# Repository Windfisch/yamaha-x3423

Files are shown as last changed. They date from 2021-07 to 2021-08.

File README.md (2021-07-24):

Faderboard Controller for a Yamaha X3423
========================================

This project takes out the X3423 motorized faderboard from a Yamaha 01v96 mixer and lets you wire it
up via USB. Additionally, it will have a display for each two faders that can display information
such as the assigned control.

Features right now:
	- Fader values are sent and received via MIDI CCs 1-17; sending a CC via MIDI will move the
	  fader to the respective position.
	- Integrating position regulator allows precise movement of the faders (which would otherwise
	  stop a bit before the actual target position due to friction).
	- Faders can work continously or in discrete steps; CCs 71-87 control the number of steps (where
	  0 means "continuous").
	- Calibration data is stored to flash. Perform a calibration by sending CC 100.

Hardware setup
--------------

Use a 1.25 pitch FFC A ribbon cable with 34 pins (*Note: these are quite difficult to get, I bought
a 40-lane-cable and cut it down.*) to connect the PCB with the faderboard on CN001; either use the
proper connector (*not JST*) to connect J12 with CN002, or solder an appropriate connector/cables to
CN002. Connect J16 and J17 to a buck/boost converter accepting 16V and outputting +15V/-15V, e.g.
DD39AJPA (DD1912PA should work too) from your favourite chinese marketplace.

Be sure to simultaneously power up both the main PSU and the USB board for now.

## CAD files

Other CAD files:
case/front_laser/front_panel.FCStd

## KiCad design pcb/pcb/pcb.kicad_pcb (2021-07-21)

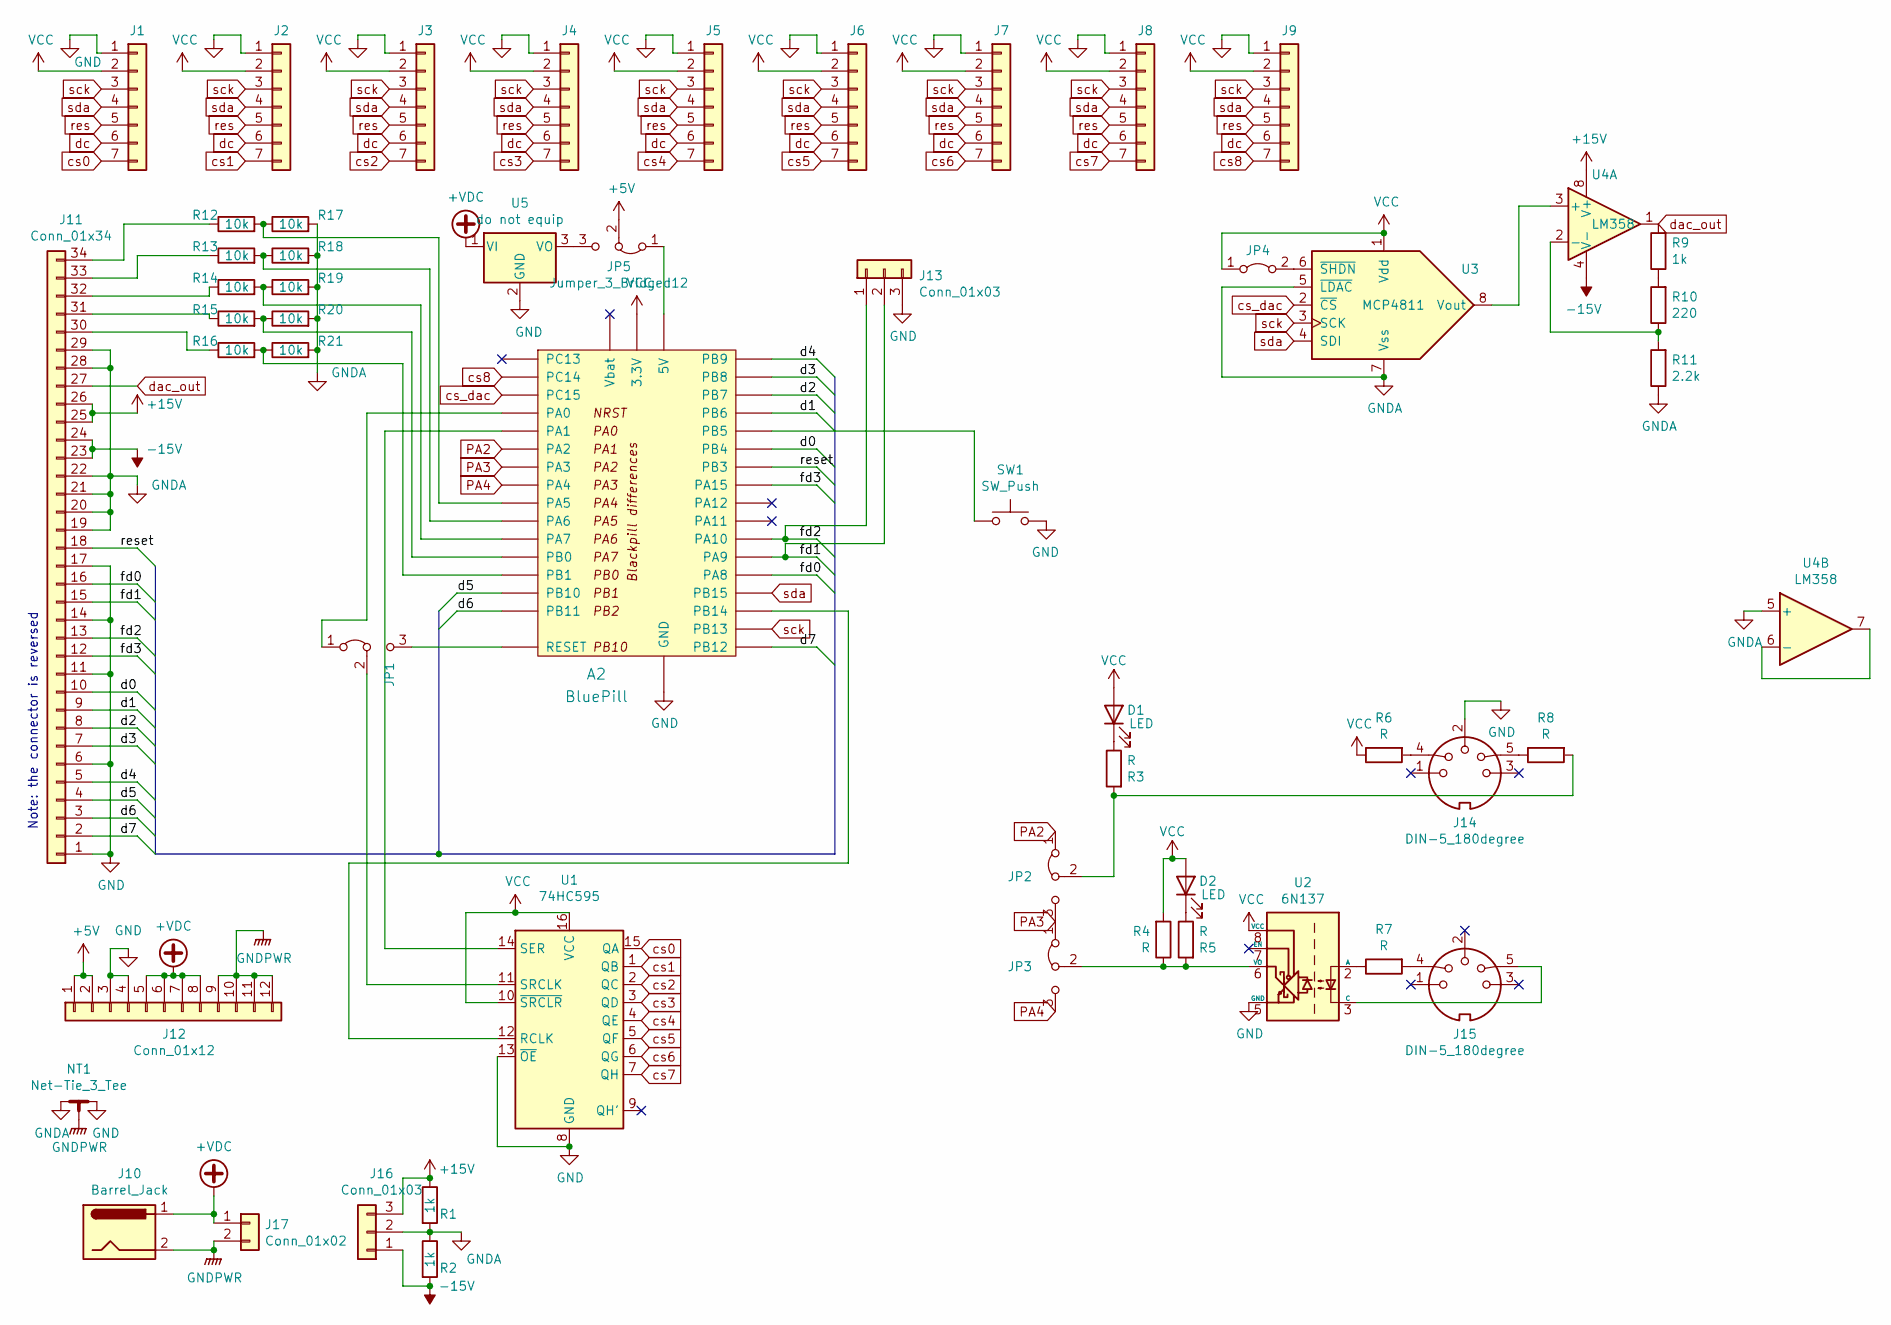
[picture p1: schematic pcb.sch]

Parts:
A2: BluePill; BLUEPILL-blackpill
D1, D2: LED; LED_D3.0mm_Horizontal_O1.27mm_Z2.0mm_IRBlack
J1, J2, J3, J4, J5, J6, J7, J8, J9: Conn_01x07; JST_XH_B7B-XH-A_1x07_P2.50mm_Vertical
J10: Barrel_Jack; BarrelJack_CUI_PJ-063AH_Horizontal
J11: Conn_01x34; Molex_52044_3445
J12: Conn_01x12; JST_PH_B12B-PH-K_1x12_P2.00mm_Vertical
J13: Conn_01x03; PinHeader_1x03_P2.54mm_Horizontal
J14, J15: DIN-5_180degree; DIN5
J16: Conn_01x03; JST_XH_B3B-XH-A_1x03_P2.50mm_Vertical
J17: Conn_01x02; JST_XH_B2B-XH-A_1x02_P2.50mm_Vertical
JP1, JP2, JP3, JP5: Jumper_3_Bridged12; SolderDipJumper3alt
JP4: Jumper_2_Bridged; SolderDipJumper2alt
NT1: Net-Tie_3_Tee; NetTie-3_SMD_Pad0.5mm
R1, R2, R9: 1k; R_0805_2012Metric
R3, R4, R5, R6, R7, R8: R; R_0805_2012Metric
R10: 220; R_0805_2012Metric
R11: 2.2k; R_0805_2012Metric
R12, R13, R14, R15, R16, R17, R18, R19, R20, R21: 10k; R_0805_2012Metric
SW1: SW_Push; SW_Tactile_Straight_KSL0Axx1LFTR
U1: 74HC595; DIP-16_W7.62mm
U2: 6N137; DIP-8_W7.62mm
U3: MCP4811; DIP-8_W7.62mm
U4: LM358; DIP-8_W7.62mm
U5: do not equip; TO-220-3_Horizontal_TabDown

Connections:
+5V: J12.1, J12.2, JP5.2 (C)
+15V: J11.25, J11.26, J16.3, R1.1, U4.8 (V+)
+VDC: J10.1, J12.5, J12.6, J12.7, J12.8, J17.1, U5.1 (VI)
-15V: J11.23, J11.24, J16.1, R2.2, U4.4 (V-)
/d0: A2.PB4, J11.10
/d1: A2.PB6, J11.9
/d2: A2.PB7, J11.8
/d3: A2.PB8, J11.7
/d4: A2.PB9, J11.5
/d5: A2.PB10, J11.4
/d6: A2.PB11, J11.3
/d7: A2.PB12, J11.2
/fd0: A2.PA8, J11.16
/fd1: A2.PA9, J11.15, J13.2
/fd2: A2.PA10, J11.13, J13.1
/fd3: A2.PA15, J11.12
/reset: A2.PB3, J11.18
GND: A2.G (GND), J1.1, J2.1, J3.1, J4.1, J5.1, J6.1, J7.1, J8.1, J9.1, J11.1, J11.6, J11.11, J11.14, J11.17, J12.3, J12.4, J13.3, J14.2, NT1.2, SW1.1, U1.8 (GND), U1.13 (~OE), U2.5 (GND), U5.2 (GND)
GNDA: J11.19, J11.20, J11.21, J11.22, J11.28, J11.29, J16.2, NT1.1, R1.2, R2.1, R11.1, R17.2, R18.2, R19.2, R20.2, R21.2, U3.5 (~LDAC), U3.7 (Vss), U4.5 (+)
GNDPWR: J10.2, J12.9, J12.10, J12.11, J12.12, J17.2, NT1.3
unnamed: A2.5V, JP5.1 (A)
unnamed: A2.NRST (RESET), JP1.3 (B)
unnamed: A2.PA0, JP1.1 (A)
unnamed: A2.PA1, U1.14 (SER)
unnamed: A2.PA5, R12.2, R17.1
unnamed: A2.PA6, R13.2, R18.1
unnamed: A2.PA7, R14.2, R19.1
unnamed: A2.PB0, R15.2, R20.1
unnamed: A2.PB1, R16.2, R21.1
unnamed: A2.PB5, SW1.2
unnamed: A2.PB14, U1.12 (RCLK)
unnamed: D1.1 (K), R3.1
unnamed: D2.1 (K), R5.1
unnamed: J11.30, R16.1
unnamed: J11.31, R15.1
unnamed: J11.32, R14.1
unnamed: J11.33, R13.1
unnamed: J11.34, R12.1
unnamed: J14.4, R6.2
unnamed: J14.5, R8.1
unnamed: J15.4, R7.2
unnamed: J15.5, U2.3 (C)
unnamed: JP1.2 (C), U1.11 (SRCLK)
unnamed: JP2.2 (C), R3.2, R8.2
unnamed: JP3.2 (C), R4.1, R5.2, U2.6 (VO)
unnamed: JP4.2 (B), U3.6 (~SHDN)
unnamed: JP5.3 (B), U5.3 (VO)
unnamed: R7.1, U2.2 (A)
unnamed: R10.1, R11.2, U4.2 (-)
unnamed: R9.1, R10.2
unnamed: U3.8 (Vout), U4.3 (+)
unnamed: U4.6 (-), U4.7
PA2: A2.PA2, JP2.1 (A)
PA3: A2.PA3, JP2.3 (B), JP3.1 (A)
PA4: A2.PA4, JP3.3 (B)
VCC: A2.3V3 (3.3V), D1.2 (A), D2.2 (A), J1.2, J2.2, J3.2, J4.2, J5.2, J6.2, J7.2, J8.2, J9.2, JP4.1 (A), R4.2, R6.1, U1.10 (~SRCLR), U1.16 (VCC), U2.8 (VCC), U3.1 (Vdd)
cs0: J1.7, U1.15 (QA)
cs1: J2.7, U1.1 (QB)
cs2: J3.7, U1.2 (QC)
cs3: J4.7, U1.3 (QD)
cs4: J5.7, U1.4 (QE)
cs5: J6.7, U1.5 (QF)
cs6: J7.7, U1.6 (QG)
cs7: J8.7, U1.7 (QH)
cs8: A2.PC14, J9.7
cs_dac: A2.PC15, U3.2 (~CS)
dac_out: J11.27, R9.2, U4.1
dc: J1.6, J2.6, J3.6, J4.6, J5.6, J6.6, J7.6, J8.6, J9.6
res: J1.5, J2.5, J3.5, J4.5, J5.5, J6.5, J7.5, J8.5, J9.5
sck: A2.PB13, J1.3, J2.3, J3.3, J4.3, J5.3, J6.3, J7.3, J8.3, J9.3, U3.3 (SCK)
sda: A2.PB15, J1.4, J2.4, J3.4, J4.4, J5.4, J6.4, J7.4, J8.4, J9.4, U3.4 (SDI)

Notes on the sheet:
Note: the connector is reversed

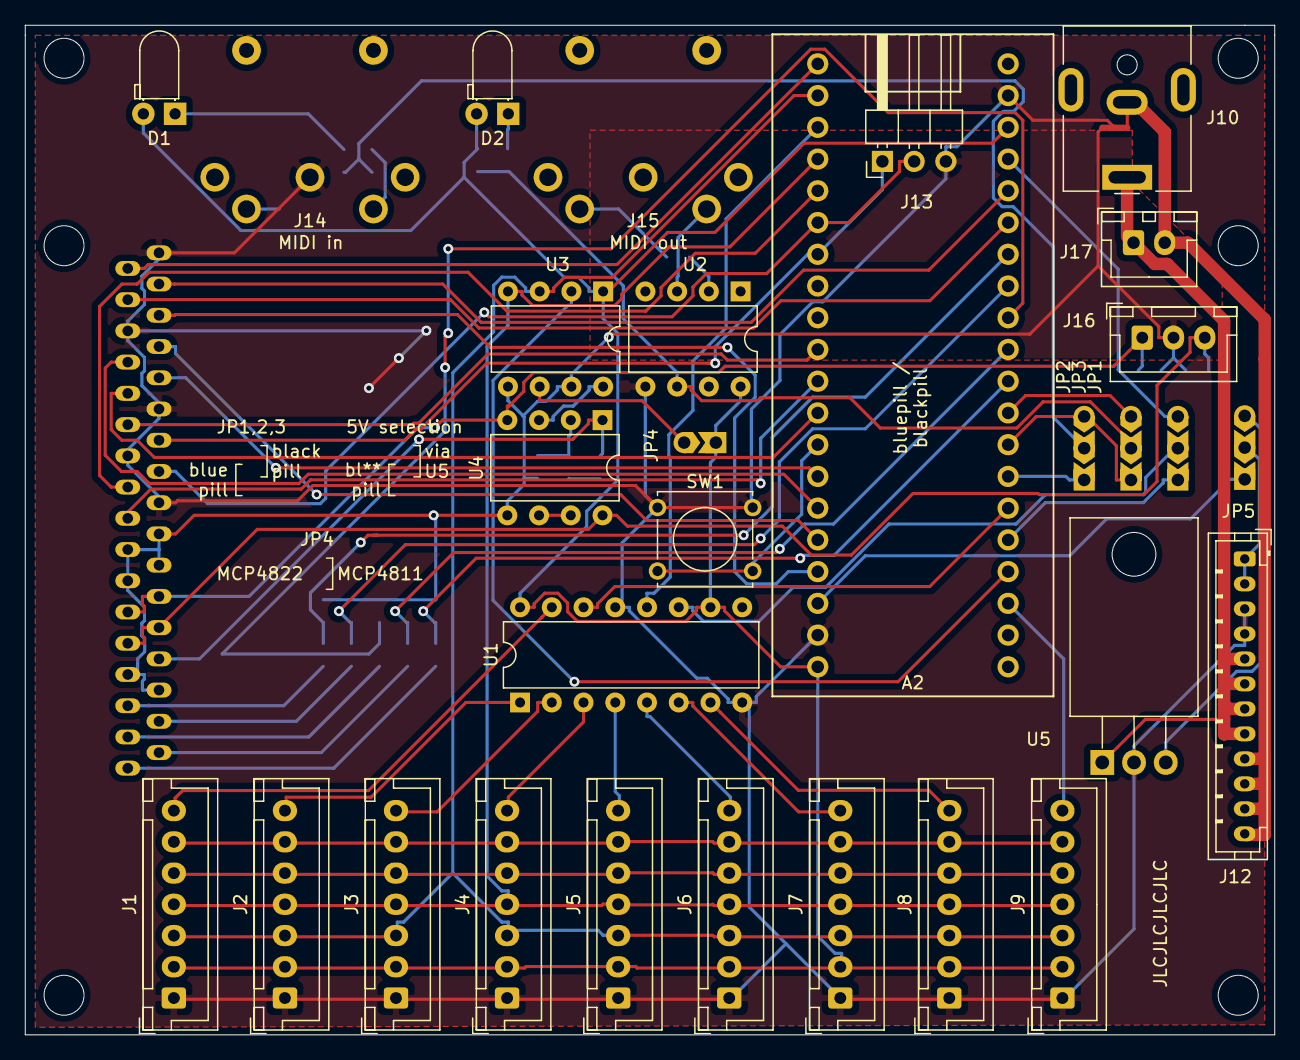
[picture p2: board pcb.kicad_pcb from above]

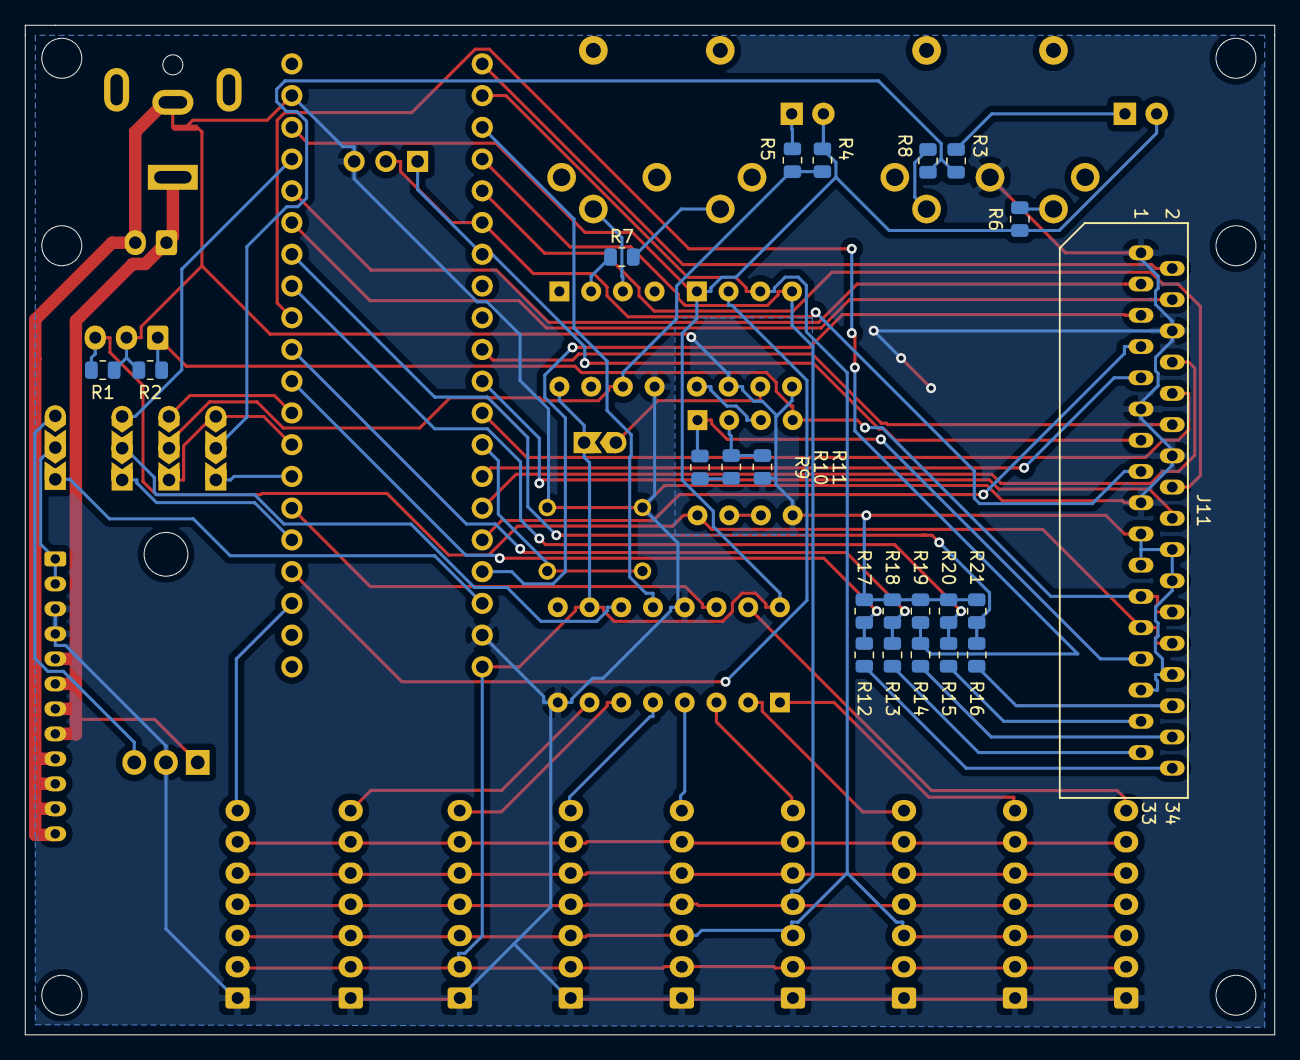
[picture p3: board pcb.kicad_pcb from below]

Board: 2 copper layers, 100.0 x 80.8 mm, 59 parts (22 on the bottom side), 71 nets.

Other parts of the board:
hole1, hole1#2, hole2, hole2#2, hole3, hole4: MountingHole_3.2mm_M3_DIN965

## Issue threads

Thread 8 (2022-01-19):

Fix laser layout

Windfisch, 2022-01-19:

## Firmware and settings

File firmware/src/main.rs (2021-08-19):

#![no_main]
#![no_std]

mod x3423;
mod fader;
use x3423::X3423;
use fader::Fader;

use embedded_hal::digital::v2::OutputPin;
use embedded_hal::digital::v1_compat::OldOutputPin;
use rtic::app;
use stm32f1xx_hal::gpio::{gpiob::*, gpioc::*, Input, Floating, Alternate, Output, PushPull, State};
use stm32f1xx_hal::spi;
use stm32f1xx_hal::timer;
use stm32f1xx_hal::prelude::*;
use stm32f1xx_hal::delay::Delay;
use stm32f1xx_hal::usb::{UsbBus, Peripheral, UsbBusType};
use stm32f1xx_hal::pac::TIM2;
use mcp49xx::Mcp49xx;
use mcp49xx::interface::SpiInterface;
use mcp49xx::marker::Resolution12Bit;
use mcp49xx::marker::DualChannel;
use mcp49xx::marker::Unbuffered;
use stm32f1xx_hal::time::Hertz;

use usb_device::prelude::*;

use micromath::F32Ext;


const BASE_CURRENT: f32 = 0.3; // Ampere
const FADER_CURRENT: f32 = 0.25; // Ampere. Note: this is only for slow movement and stall. Large jumps draw more current!
const CURRENT_LIMIT: f32 = 3.33; // Ampere.
const MAX_ACTIVE_FADERS: u16 = ((CURRENT_LIMIT - BASE_CURRENT) / FADER_CURRENT) as u16;
const MAX_ACTIVE_FADERS_DURING_CALIBRATION: u16 = 3;


#[panic_handler]
fn panic(_: &core::panic::PanicInfo) -> ! {
	use core::mem::MaybeUninit;
	cortex_m::interrupt::disable();

	let led: stm32f1xx_hal::gpio::gpioc::PC13<Input<Floating>> = unsafe { MaybeUninit::uninit().assume_init() };
	let mut reg = unsafe { MaybeUninit::uninit().assume_init() };
	let mut led = led.into_push_pull_output(&mut reg);
	loop {
		let mut blink_thrice = |delay: u32| {
			for _ in 0..3 {
				led.set_low().ok();
				cortex_m::asm::delay(5000000*delay);
				led.set_high().ok();
				cortex_m::asm::delay(10000000);
			}
			cortex_m::asm::delay(10000000);
		};
		blink_thrice(1);
		blink_thrice(4);
		blink_thrice(1);
		cortex_m::asm::delay(10000000);
	}
}

#[derive(Clone, Copy, PartialEq)]
pub enum Calib
{
	Pending,
	Running,
	Idle
}

#[derive(Clone, Copy)]
pub enum FaderState {
	Idle,
	UserControlled,
	UserOverride,
	MidiControlledSlow,
	MidiControlledJump
}

#[derive(Clone, Copy)]
pub struct Queue {
	history: [u16; 64],
	pointer: usize,
	counter: u16
}

impl Queue {
	const SPARSITY: u16 = 24;
	pub const fn new() -> Queue { Queue { history: [0; 64], pointer: 0, counter: 0 } }

	fn u16_to_f32(value: u16) -> f32 {
		value as f32 / 65535.0
	}

	pub fn push(&mut self, value: f32) {
		if self.counter == 0 {
			self.history[self.pointer] = (value * 65535.0) as u16;
			self.pointer = (self.pointer + 1) % self.history.len();
		}
		self.counter = (self.counter + 1) % Self::SPARSITY;
	}
	pub fn delta(&self) -> f32 {
		Self::u16_to_f32(*self.history.iter().max().unwrap()) - Self::u16_to_f32(*self.history.iter().min().unwrap())
	}

	pub fn trend(&self) -> f32 {
		let most_recent_pointer = (self.pointer + self.history.len() - 1) % self.history.len();
		return Self::u16_to_f32(self.history[most_recent_pointer]) - Self::u16_to_f32(self.history[self.pointer]);
	}
}

#[derive(Copy,Clone)]
pub struct FaderStateMachine {
	state: FaderState,
	old_setpoint: f32,
	stable_timer: u32,
	jump_count: u32,
	measured_history: Queue,
	setpoint_history: Queue,
}

pub struct FaderResult {
	pub fader_move_target: Option<f32>,
	pub midi_send_value: Option<f32>
}

trait Signum {
	fn signum(self) -> Self;
}

impl Signum for f32 {
	fn signum(self) -> f32 {
		if self > 0.0 { return 1.0; }
		else if self < 0.0 { return -1.0; }
		else { return 0.0; }
	}
}

impl FaderStateMachine {
	pub const fn new() -> FaderStateMachine {
		FaderStateMachine {
			state: FaderState::Idle,
			old_setpoint: 0.5,
			stable_timer: 0,
			jump_count: 0,
			measured_history: Queue::new(),
			setpoint_history: Queue::new()
		}
	}
	pub fn process(&mut self, setpoint: f32, measured: f32) -> FaderResult {
		let JUMP_THRESHOLD = 3.0;
		let SET_DEADZONE = 0.01;
		let SETPOINT_DEADZONE = 0.001;
		let ESCAPE_LIMIT = 0.2;
		let INPUT_DEADZONE = 0.05;
		let INPUT_DEADZONE_WHEN_MIDI_CONTROLLED = 0.15;
		let CAPTURE_ZONE = 0.06;
		let STABILIZE_TIMEOUT = 500;
		let JUMP_TIMEOUT = 2000;

		self.measured_history.push(measured);
		self.setpoint_history.push(setpoint);

		if (setpoint - measured).abs() < CAPTURE_ZONE {
			self.stable_timer = self.stable_timer.saturating_add(1);
		}
		else {
			self.stable_timer = 0;
		}

		let setpoint_diff = (self.old_setpoint - setpoint).abs();
		if setpoint_diff > SETPOINT_DEADZONE {
			self.stable_timer = 0;
			self.old_setpoint = setpoint;
		}

		match self.state {
			FaderState::Idle => {
				if setpoint_diff >= JUMP_THRESHOLD {
					self.state = FaderState::MidiControlledJump;
					self.jump_count = 0;
				}
				else if setpoint_diff > SETPOINT_DEADZONE {
					self.state = FaderState::MidiControlledSlow;
				}
			
				if (setpoint - measured).abs() >= ESCAPE_LIMIT {
					self.state = FaderState::UserOverride;
					self.measured_history.push(1.0);
					self.measured_history.push(0.0);
				}
				else if (setpoint - measured).abs() >= INPUT_DEADZONE {
					self.state = FaderState::UserControlled;
					self.measured_history.push(1.0);
					self.measured_history.push(0.0);
				}
				
				FaderResult {
					fader_move_target: None,
					midi_send_value: None
				}
			}
			FaderState::MidiControlledSlow => {
				if setpoint_diff >= JUMP_THRESHOLD {
					self.state = FaderState::MidiControlledJump;
					self.jump_count = 0;
				}
				if self.stable_timer >= STABILIZE_TIMEOUT {
					self.state = FaderState::Idle;
				}
				if (setpoint - measured).abs() >= ESCAPE_LIMIT {
					self.state = FaderState::UserOverride;
					self.measured_history.push(1.0);
					self.measured_history.push(0.0);
				}
				else if (setpoint - measured).abs() >= INPUT_DEADZONE_WHEN_MIDI_CONTROLLED {
					self.state = FaderState::UserControlled;
					self.measured_history.push(1.0);
					self.measured_history.push(0.0);
				}

				FaderResult {
					fader_move_target: Some(setpoint),
					midi_send_value: None
				}
			}
			FaderState::MidiControlledJump => {
				if self.stable_timer >= STABILIZE_TIMEOUT {
					self.state = FaderState::Idle;
				}
				if self.jump_count >= JUMP_TIMEOUT {
					self.state = FaderState::Idle;
				}
				self.jump_count += 1;

				FaderResult {
					fader_move_target: Some(setpoint),
					midi_send_value: None
				}
			}
			FaderState::UserControlled => {
				let expected_trend_signum = (measured - setpoint).signum();
				if self.measured_history.delta() < INPUT_DEADZONE {
					if (setpoint - measured).abs() < SET_DEADZONE {
						self.state = FaderState::Idle;
					}
					else if self.setpoint_history.trend().signum() != expected_trend_signum || self.setpoint_history.delta() < SET_DEADZONE {
						self.state = FaderState::MidiControlledJump;
						self.jump_count = 0;
					}
				}
				
				if (setpoint - measured).abs() >= ESCAPE_LIMIT {
					self.state = FaderState::UserOverride;
				}

				let fader_move_target =
					if (setpoint - measured).abs() < CAPTURE_ZONE {
						None
					}
					else {
						let limit = setpoint + CAPTURE_ZONE * (measured - setpoint).signum();
						Some( limit.clamp(0.0, 1.0) )
					};

				FaderResult {
					fader_move_target,
					midi_send_value: Some(measured)
				}
			}
			FaderState::UserOverride => {
				let expected_trend_signum = (measured - setpoint).signum();
				if self.measured_history.delta() < INPUT_DEADZONE {
					if (setpoint - measured).abs() < SET_DEADZONE {
						self.state = FaderState::Idle;
					}
					else if self.setpoint_history.trend().signum() != expected_trend_signum || self.setpoint_history.delta() < SET_DEADZONE {
						self.state = FaderState::MidiControlledJump;
						self.jump_count = 0;
					}
				}

				FaderResult {
					fader_move_target: None,
					midi_send_value: Some(measured)
				}
			}
		}
	}
}

#[derive(Copy,Clone)]
pub struct SlewTarget {
	target_value: f32,
	current_value: f32,
}

impl SlewTarget {
	pub fn new() -> SlewTarget { SlewTarget { target_value: 0.5, current_value: 0.0 } }
	pub fn set_target(&mut self, value: f32) {
		self.target_value = value;
	}
	pub fn slew_value(&mut self) -> f32 {
		if self.current_value > self.target_value {
			self.current_value = (self.current_value - 0.002).clamp(self.target_value, 1.0);
		}
		else if self.current_value < self.target_value {
			self.current_value = (self.current_value + 0.002).clamp(0.0, self.target_value);
		}
		return self.current_value;
	}
}

pub struct MidiSender {
	last_values: [f32; 17]
}
impl MidiSender {
	pub fn new() -> MidiSender { MidiSender { last_values: [-1.0; 17] } }
	pub fn send_midi_cc(&mut self, idx: usize, value: f32, midi: &mut usbd_midi::midi_device::MidiClass<'static, UsbBus<Peripheral>>) {
		let cc_number = idx as u8 + 1;
		if (self.last_values[idx] - value).abs() > 0.005 {
			let val = (value * 16383.0) as u16;
			let lsb = (val % 128) as u8;
			let msb = (val / 128) as u8;
			
			if midi.send_bytes(&[0x0B, 0xB0, cc_number + 32, lsb, 0x0B, 0xB0, cc_number, msb]).is_ok() {
				self.last_values[idx] = value;
			}
		}
	}
}



#[derive(Clone, Copy)]
pub enum FaderConfig {
	Continuous,
	Steps(u8),
	Bidirectional,
}

#[app(device = stm32f1xx_hal::pac, peripherals = true)]
const APP: () = {
	struct Resources {
		delay: stm32f1xx_hal::delay::Delay,
		mytimer: timer::CountDownTimer<TIM2>,

		led: PC13<Output<PushPull>>,

		usb_dev: UsbDevice<'static, UsbBusType>,
		midi: usbd_midi::midi_device::MidiClass<'static, UsbBus<Peripheral>>,
		dac: Mcp49xx<SpiInterface<spi::Spi<stm32f1xx_hal::pac::SPI2, spi::Spi2NoRemap, (PB13<Alternate<PushPull>>, spi::NoMiso, PB15<Alternate<PushPull>>), u8>, OldOutputPin<PC15<Output<PushPull>>>>, Resolution12Bit, DualChannel, Unbuffered>,

		x3423: X3423,

		faders: [Fader; 17],
		fader_config: [FaderConfig; 17],
		fader_midi_commands: [Option<f32>; 17],
		fader_processes_midi_command: [bool; 17],
		calibration_request: Calib,

		flash: stm32f1xx_hal::flash::Parts,

		midi_sender: MidiSender,
		fader_bidir: [FaderStateMachine; 17],
		fader_bidir_target: [SlewTarget; 17]
	}

	#[init]
	fn init(cx: init::Context) -> init::LateResources {
		static mut USB_BUS: Option<usb_device::bus::UsbBusAllocator<UsbBusType>> = None;

		// Enable cycle counter
		let mut core = cx.core;
		core.DWT.enable_cycle_counter();

		let device: stm32f1xx_hal::stm32::Peripherals = cx.device;

		// Setup clocks
		let mut flash = device.FLASH.constrain();
		let mut rcc = device.RCC.constrain();
		let mut afio = device.AFIO.constrain(&mut rcc.apb2);
		let clocks = rcc
			.cfgr
			.use_hse(8.mhz())
			.sysclk(72.mhz())
			.pclk1(36.mhz())
			.freeze(&mut flash.acr);

		let delay = Delay::new(core.SYST, clocks);

		// Setup LED
		let mut gpioa = device.GPIOA.split(&mut rcc.apb2);
		let mut gpiob = device.GPIOB.split(&mut rcc.apb2);
		let mut gpioc = device.GPIOC.split(&mut rcc.apb2);
		let (pa15, pb3, pb4) = afio.mapr.disable_jtag(gpioa.pa15, gpiob.pb3, gpiob.pb4);
		let mut led = gpioc
			.pc13
			.into_push_pull_output_with_state(&mut gpioc.crh, State::Low);
		led.set_low().unwrap();

		// Configure USB
		// BluePill board has a pull-up resistor on the D+ line.
		// Pull the D+ pin down to send a RESET condition to the USB bus.
		let mut usb_dp = gpioa.pa12.into_push_pull_output(&mut gpioa.crh);
		usb_dp.set_low().ok();
		cortex_m::asm::delay(clocks.sysclk().0 / 100);
		
		let usb_dm = gpioa.pa11;
		let usb_dp = usb_dp.into_floating_input(&mut gpioa.crh);

		let usb_pins = Peripheral {
			usb: device.USB,
			pin_dm: usb_dm,
			pin_dp: usb_dp
		};
		*USB_BUS = Some( UsbBus::new(usb_pins) );
		let usb_bus = USB_BUS.as_ref().unwrap();

		let midi = usbd_midi::midi_device::MidiClass::new(usb_bus, 1, 1).unwrap();
		let usb_dev = UsbDeviceBuilder::new(usb_bus, UsbVidPid(0x16c0, 0x27dd))
			.manufacturer("Windfisch")
			.product("Faderboard")
			.serial_number("000000")
			.device_class(usbd_midi::data::usb::constants::USB_CLASS_NONE)
			.build();

		// Configure SPI
		let mosi = gpiob.pb15.into_alternate_push_pull(&mut gpiob.crh);
		let sck = gpiob.pb13.into_alternate_push_pull(&mut gpiob.crh);
		let dac_cs: OldOutputPin<_> = gpioc.pc15.into_push_pull_output_with_state(&mut gpioc.crh, State::High).into();

		let spi = spi::Spi::spi2(device.SPI2, (sck, spi::NoMiso, mosi), spi::Mode { phase : spi::Phase::CaptureOnFirstTransition, polarity : spi::Polarity::IdleLow }, 5.mhz(), clocks, &mut rcc.apb1);
		let dac = mcp49xx::Mcp49xx::new_mcp4822(spi, dac_cs);

		let adc = stm32f1xx_hal::adc::Adc::adc1(device.ADC1, &mut rcc.apb2, clocks);

		let mut mytimer =
			timer::Timer::tim2(device.TIM2, &clocks, &mut rcc.apb1)
			.start_count_down(Hertz(1000));
		mytimer.listen(timer::Event::Update);

		let mut resources = init::LateResources {
			led,
			x3423: X3423::new(x3423::X3423Resources {
				mfpos0: gpioa.pa5.into_analog(&mut gpioa.crl),
				mfpos1: gpioa.pa6.into_analog(&mut gpioa.crl),
				mfpos2: gpioa.pa7.into_analog(&mut gpioa.crl),
				mfpos3: gpiob.pb0.into_analog(&mut gpiob.crl),
				mfpos4: gpiob.pb1.into_analog(&mut gpiob.crl),
				reset: pb3.into_open_drain_output_with_state(&mut gpiob.crl, State::Low),
				fd0: gpioa.pa8.into_open_drain_output(&mut gpioa.crh),
				fd1: gpioa.pa9.into_open_drain_output(&mut gpioa.crh),
				fd2: gpioa.pa10.into_open_drain_output(&mut gpioa.crh),
				fd3: pa15.into_open_drain_output(&mut gpioa.crh),
				data: x3423::X3423DataPins {
					d0: pb4.into_open_drain_output(&mut gpiob.crl),
					d1: gpiob.pb6.into_open_drain_output(&mut gpiob.crl),
					d2: gpiob.pb7.into_open_drain_output(&mut gpiob.crl),
					d3: gpiob.pb8.into_open_drain_output(&mut gpiob.crh),
					d4: gpiob.pb9.into_open_drain_output(&mut gpiob.crh),
					d5: gpiob.pb10.into_open_drain_output(&mut gpiob.crh),
					d6: gpiob.pb11.into_open_drain_output(&mut gpiob.crh),
					d7: gpiob.pb12.into_open_drain_output(&mut gpiob.crh),
				},
				adc,
			}),
			usb_dev,
			midi,
			dac,
			delay,
			faders: Default::default(),
			fader_midi_commands: [None; 17],
			mytimer,
			fader_config: [FaderConfig::Bidirectional; 17],
			fader_processes_midi_command: [false; 17],
			flash,
			calibration_request: Calib::Idle,
			midi_sender: MidiSender::new(),
			fader_bidir: [FaderStateMachine::new(); 17],
			fader_bidir_target: [SlewTarget::new(); 17]
		};

		
		let writer = resources.flash.writer(stm32f1xx_hal::flash::SectorSize::Sz2K, stm32f1xx_hal::flash::FlashSize::Sz128K);
		for i in 0..17 {
			let params = writer.read(65536-2048 + 10*i, 10).unwrap();
			if params[0] != 0xFF && params[1] != 0xFF {
				resources.faders[i as usize].set_calibration_data(params);
			}
		}

		resources.x3423.reset();

		resources
	}

	
	#[task(binds = TIM2, resources = [x3423, dac, delay, faders, fader_midi_commands, mytimer, led, midi, fader_config, fader_processes_midi_command, calibration_request, flash, midi_sender, fader_bidir, fader_bidir_target], priority=1)]
	fn xmain(mut c : xmain::Context) {
		static mut BLINK: u64 = 0;

		let res = &mut c.resources;
		res.mytimer.clear_update_interrupt_flag();
		
		*BLINK += 1;
		if (*BLINK) % 100 == 0 {
			res.led.toggle().unwrap();
		}

		let calibration_state = res.calibration_request.lock(|c|*c);

		let fader_midi_commands = res.fader_midi_commands.lock(|fader_midi_commands| {
			let tmp = *fader_midi_commands;
			*fader_midi_commands = [None; 17];
			tmp
		});

		// read raw fader values
		let faders = &mut res.faders;
		res.x3423.read_values(|idx, value| { faders[idx].update_value(value) }, res.delay);

		// do all the fader processing
		if calibration_state == Calib::Idle {
			let faders = &mut res.faders;
			let fader_config = res.fader_config.lock(|s| *s);
			for i in 0..17 {
				match fader_config[i] {
					FaderConfig::Steps(steps) => {
						if !res.fader_processes_midi_command[i] {
							let steps_f32 = steps as f32;
							let quantized_value = (faders[i].live_value() * (steps_f32 - 1.)).round() / (steps_f32 - 1.);
							let diff = faders[i].live_value() - quantized_value;

							if diff.abs() >= 0.02 {
								faders[i].set_target(quantized_value);
							}
						}
						
						let midi_sender = &mut res.midi_sender;
						res.midi.lock(|midi| midi_sender.send_midi_cc(i, faders[i].value(), midi));

						if let Some(target) = fader_midi_commands[i] {
							faders[i].set_target(target);
							res.fader_processes_midi_command[i] = true;
						}
					}
					FaderConfig::Bidirectional => {
						if let Some(value) = fader_midi_commands[i] {
							res.fader_bidir_target[i].set_target(value);
						}

						let result = res.fader_bidir[i].process(res.fader_bidir_target[i].slew_value(), faders[i].live_value());

						if let Some(value) = result.midi_send_value {
							let midi_sender = &mut res.midi_sender;
							res.midi.lock(|midi| midi_sender.send_midi_cc(i, value, midi));
						}

						if let Some(target) = result.fader_move_target {
							faders[i].set_target(target);
						}
						else {
							faders[i].clear_target();
						}
					}
					FaderConfig::Continuous => {
						let midi_sender = &mut res.midi_sender;
						res.midi.lock(|midi| midi_sender.send_midi_cc(i, faders[i].value(), midi));
						
						if let Some(target) = fader_midi_commands[i] {
							faders[i].set_target(target);
						}
					}
				}
			}
		}


		// set fader values, handle movement and calibration
		let mut active_faders = 0;
		let mut n_active_faders = 0;
		let fader_limit = match res.calibration_request.lock(|c|*c) {
			Calib::Idle => MAX_ACTIVE_FADERS,
			_ => MAX_ACTIVE_FADERS_DURING_CALIBRATION
		};
		
		for (i, (fader, processes_midi)) in
			res.faders.iter_mut()
			.zip(res.fader_processes_midi_command.iter_mut())
			.enumerate()
		{
			// set values received via MIDI and process fader movement / calibration
			if n_active_faders < fader_limit
			{
				if let Some(target_value) = fader.process() {
					active_faders |= 1 << i;
					n_active_faders += 1;

					res.dac.send(mcp49xx::Command::default().double_gain().channel(mcp49xx::Channel::Ch0).value(target_value)).unwrap();
					res.delay.delay_us(5_u16);
					res.x3423.capture_analog_value(i as u8, res.delay);
				}
			}
			
			if fader.target().is_none() {
				*processes_midi = false;
			}
		}
		res.x3423.set_motor_enable(active_faders);


		// handle pending calibration request or write finished calibration to flash
		match res.calibration_request.lock(|c| *c)
		{
			Calib::Running => {
				if !res.faders.iter().any(|fader| fader.is_calibrating()) {
					// save to flash
					let mut data: [u8; 170] = [0; 170];
					for i in 0..17 {
						let calib = res.faders[i].get_calibration_data();
						for j in 0..10 {
							data[i*10 + j] = calib[j];
						}
					}

					let mut writer = res.flash.writer(stm32f1xx_hal::flash::SectorSize::Sz2K, stm32f1xx_hal::flash::FlashSize::Sz128K);
					writer.change_verification(false);
					writer.erase(65536-2048, 2*1024).unwrap();
					writer.write(65536-2048, &data).unwrap();

					res.calibration_request.lock(|c| *c = Calib::Idle);
				}
			}
			Calib::Pending => {
				for fader in res.faders.iter_mut() {
					fader.start_calibration();
				}
				res.calibration_request.lock(|c| *c = Calib::Running);
			}
			Calib::Idle => {}
		}
	}

	#[task(binds = USB_LP_CAN_RX0, resources=[midi, usb_dev, fader_midi_commands, fader_config, calibration_request], priority=2)]
	fn periodic_usb_poll(c : periodic_usb_poll::Context) {
		static mut LSB: [u8; 17] = [0; 17];

		c.resources.usb_dev.poll(&mut[c.resources.midi]);

		let mut buffer = [0u8; 128];
		while let Ok(len) = c.resources.midi.read(&mut buffer) {
			for message in buffer[0..len].chunks(4) {
				if message.len() == 4 {
					//let cable = (message[0] & 0xF0) >> 4;
					let messagetype = message[0] & 0x0F;

					match messagetype {
						0xB => {
							//let channel = message[1] & 0x0F;
							let cc = message[2];
							let value = message[3];
							if (1..=17).contains(&cc) {
								c.resources.fader_midi_commands[(cc-1) as usize] = Some( (((value as u16) << 7) + LSB[(cc-1) as usize] as u16) as f32 / 16384.0);
							}
							if (33..=49).contains(&cc) {
								LSB[cc as usize - 33] = value;
							}

							if (71..87).contains(&cc) {
								c.resources.fader_config[(cc-71) as usize] =
									match value {
										0 => FaderConfig::Continuous,
										127 => FaderConfig::Bidirectional,
										steps => FaderConfig::Steps(steps)
									};
							}

							if cc == 100 {
								*c.resources.calibration_request = Calib::Pending;
							}
						}
						_ => {}
					}
				}
			}
		}

		
	}
	
	extern "C" {
		fn EXTI0();
		fn EXTI1();
	}
};

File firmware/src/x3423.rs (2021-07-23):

use embedded_hal::digital::v2::OutputPin;
use stm32f1xx_hal::gpio::{gpioa::*, gpiob::*, Analog, Output, OpenDrain};
use stm32f1xx_hal::prelude::*;
use stm32f1xx_hal::adc::Adc;
use stm32f1xx_hal::pac::ADC1;
use core::convert::Infallible;

pub struct X3423DataPins {
	pub d0: PB4<Output<OpenDrain>>,
	pub d1: PB6<Output<OpenDrain>>,
	pub d2: PB7<Output<OpenDrain>>,
	pub d3: PB8<Output<OpenDrain>>,
	pub d4: PB9<Output<OpenDrain>>,
	pub d5: PB10<Output<OpenDrain>>,
	pub d6: PB11<Output<OpenDrain>>,
	pub d7: PB12<Output<OpenDrain>>,
}

pub struct X3423 {
	res: X3423Resources
}

pub struct X3423Resources {
	pub mfpos0: PA5<Analog>,
	pub mfpos1: PA6<Analog>,
	pub mfpos2: PA7<Analog>,
	pub mfpos3: PB0<Analog>,
	pub mfpos4: PB1<Analog>,
	pub reset: PB3<Output<OpenDrain>>,
	pub fd0: PA8<Output<OpenDrain>>,
	pub fd1: PA9<Output<OpenDrain>>,
	pub fd2: PA10<Output<OpenDrain>>,
	pub fd3: PA15<Output<OpenDrain>>,
	pub data: X3423DataPins,
	pub adc: Adc<ADC1>,
}

trait OutputPinExt {
	type Error;
	fn set(&mut self, is_high: bool) -> Result<(), Self::Error>;
}

impl<T: OutputPin> OutputPinExt for T {
	type Error = T::Error;
	fn set(&mut self, is_high: bool) -> Result<(), T::Error> {
		if is_high {
			self.set_high()
		}
		else {
			self.set_low()
		}
	}
}

fn wait() {
	cortex_m::asm::delay(10);
}

impl X3423DataPins {
	fn write_data(&mut self, data: u8) -> Result<(), Infallible> {
		self.d0.set(data & 0x01 != 0)?;
		self.d1.set(data & 0x02 != 0)?;
		self.d2.set(data & 0x04 != 0)?;
		self.d3.set(data & 0x08 != 0)?;
		self.d4.set(data & 0x10 != 0)?;
		self.d5.set(data & 0x20 != 0)?;
		self.d6.set(data & 0x40 != 0)?;
		self.d7.set(data & 0x80 != 0)?;
		Ok(())
	}
	
	fn apply_data(&mut self, data: u8, fd_pin: &mut impl embedded_hal::digital::v2::OutputPin) {
		self.write_data(data).unwrap();
		wait();
		fd_pin.set_high().ok();
		wait();
		fd_pin.set_low().ok();
	}
}

impl X3423 {
	pub fn new(res: X3423Resources) -> X3423 {
		X3423 { res }
	}

	pub fn reset(&mut self) {
		self.res.reset.set_low().ok();
		cortex_m::asm::delay(5);
		self.res.reset.set_high().ok();
	}

	pub fn set_motor_enable(&mut self, state: u32) {
		self.res.data.apply_data((state & 0xFF) as u8, &mut self.res.fd0);
		self.res.data.apply_data(((state >> 8) & 0xFF) as u8, &mut self.res.fd1);
		self.res.data.apply_data(((state >> 16) & 0x01) as u8, &mut self.res.fd2);
	}

	fn set_other(&mut self, dasel: u8, dainh: u8, adsel: u8) {
		self.res.data.apply_data((dasel & 7) | ((dainh & 7) << 3) | ((adsel & 3) << 6), &mut self.res.fd3);
	}

	pub fn capture_analog_value(&mut self, index: u8, delay: &mut impl embedded_hal::blocking::delay::DelayUs<u32>) {
		assert!(index < 17);
		let dasel = index & 7;
		let dainh = !(1 << (index >> 3));
		let adsel = 0;
		self.set_other(dasel, dainh, adsel);
		delay.delay_us(20);
		self.set_other(dasel, 7, adsel);
	}

	pub fn select_analog_value(&mut self, index: u8, delay: &mut impl embedded_hal::blocking::delay::DelayUs<u32>) {
		assert!(index < 4);
		self.set_other(0, 7, index);
		delay.delay_us(20);
	}

	pub fn read_values(&mut self, mut callback: impl FnMut(usize, u16), delay: &mut impl embedded_hal::blocking::delay::DelayUs<u32>) {
		for i in 0..4 {
			self.select_analog_value(i as u8, delay);
			callback(0 + i, self.res.adc.read(&mut self.res.mfpos0).unwrap());
			callback(4 + i, self.res.adc.read(&mut self.res.mfpos1).unwrap());
			callback(8 + i, self.res.adc.read(&mut self.res.mfpos2).unwrap());
			callback(12 +i, self.res.adc.read(&mut self.res.mfpos3).unwrap());
		}
		callback(16, self.res.adc.read(&mut self.res.mfpos4).unwrap());
	}
}

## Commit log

2021-06-16 Maybe finished PCB layout
    [pcb.kicad_pcb, pcb.sch]
2021-07-21 fix hardware bug
    [pcb.kicad_pcb, pcb.sch]
2021-07-23 input calibration
2021-07-23 Turn mainloop into periodic interrupt
2021-07-23 output calibration
2021-07-23 PI-regulator for the position
2021-07-24 Save calibration data to flash
2021-08-18 do not overwrite the calibration data when flashing
2021-08-18 work around flash bug
    [main.rs]
2021-08-18 Fix calibration bug and improve motor limiter
    [main.rs]
2021-08-18 Only process faders when not calibrating
2021-08-19 Fix most bugs (hopefully)
    [main.rs]
2021-08-19 commented out state inertia (does not work)
    [main.rs]
2021-08-19 tune fader pid
2021-08-19 Revert "commented out state inertia (does not work)"
    This reverts commit d4947a1c5d31e7677b48b715f2da753856834bb9.
    [main.rs]
2021-08-19 Revert "tune fader pid"
    This reverts commit 52b091be73a6b15411318ec79f1637854290e2f0.
2022-01-13 First case drawings
    [front_panel.FCStd]
2022-01-13 Reference drawing
    [front_panel.FCStd]
2022-01-13 Intermediate commit
    [front_panel.FCStd]
2022-01-14 laser svg file;
